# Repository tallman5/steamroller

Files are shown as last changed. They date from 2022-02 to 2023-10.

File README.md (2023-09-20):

# Steamroller

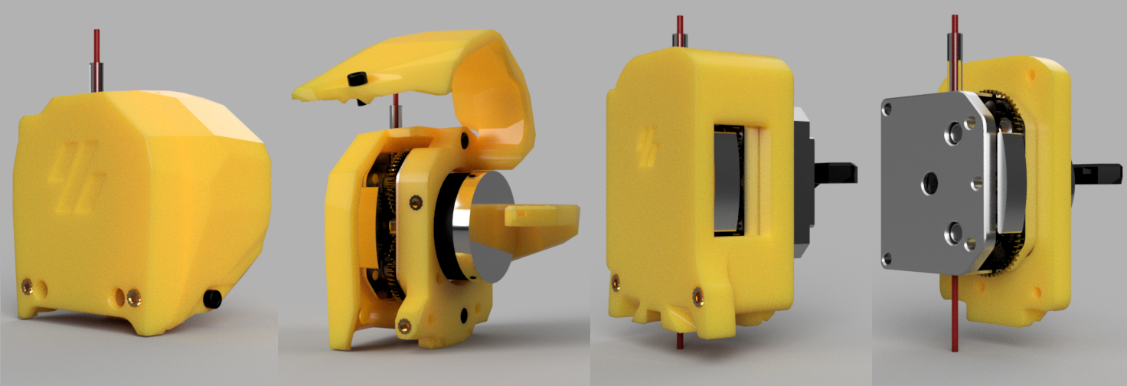
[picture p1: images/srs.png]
OMG Extruder and Steamroller Parts Steamroller


<div style='border: 1px solid #997404; border-radius: 5px; background-color: #fff3cd; padding: 15px; color: #997404;'>
   <strong>Note: </strong>These are still in testing. Please use at your own risk. Create an issue if needed. Thanks!
</div>

## Overview
The Steamroller is a custom adapter to hold the OMG Extruder for various print heads.
The following is a list of the available flavors.

1. Steamroller Stealthburner, SRSB, for the Stealthburner/Clockwork 2
1. Steamroller Afterburner, SRAB, for the Afterburner/Clockwork 1
1. Steamroller EVA, SREVA, you guessed it, for EVA, coming soon!

Print the files in the STL folder for the appropriate version.
The default STLs have a 4.7mm hole for M3x5x4 threaded inserts.
Since the inserts aren't always easy to get, there are subfolders for other size threaded inserts.
For example, the STLs in the folder ti-5-3 has 5.3mm holes for M3x5.5x4 inserts.
Want a different threaded insert size?
Create an issue here and I can create a custom set.

## OMG Extruder Links

This project does not have a donate button.
However, if you order the OMG with an affiliate link, you won't pay more and a small commission will go to this project.
Thank you!

Affiliate Link: [https://amzn.to/48pWOVK](https://amzn.to/48pWOVK)

## Why?
During a Voron 2.4 build, I was using the OMG with a bowden tube on the Voron until the Galileo parts came in.
There were some great prints coming from the OMG extruder.
After installing and tuning the Galileo, I noticed how close the prints were in quality.
So, decided to try to go direct drive with the OMG.
The Steamroller AB is the result.

## Installation Steps
Everything about this is per the Voron standard, slicer settings, heat set inserts, etc..

1. Gather parts from the BOM, there's a BOM for each flavor
1. Print the parts
   1. Yellow's not required :smile:, just used it on renders following the Steamroller theme
   1. Front and back found in the STL folder
   1. The 2- or 3- hole chain anchor from the Voron Clockwork 2 found [here](https://github.com/VoronDesign/Voron-Stealthburner/tree/main/STLs/Clockwork2)
   1. If using the SRSB, the cable cover from the Voron Clockwork 2 found [here](https://github.com/VoronDesign/Voron-Stealthburner/tree/main/STLs/Clockwork2)
1. Add the heat set inserts
1. Install the cable chain anchor to the back
1. For the SRSB, install the cable cover to the back
1. If installing a NEMA17 on the SRAB, push the motor through the back before attaching the motor to the OMG
1. Place the OMG in the Steamroller front
1. Screw the back to the front
1. Install a piece of PTFE for the Steamroller to the hotend
   1. SRAB - Mine was 62mm for a v6 hot end
1. Mount the Steamroller to the carriage
1. Install the fan assembly
1. Edit the printer.cfg, below is what I used with Klipper/Fluiddd/Spider v1.2:
      ```
      # Steamroller AB (SB and EVA should be similar)
     rotation_distance: 47.77753134
     microsteps: 16
     full_steps_per_rotation: 760
     gear_ratio: 3:1
     dir_pin: PD6
     ```
1. Do the e-steps calibration and update the rotation_distance
1. Print something!

## How Well Does It Work?
In the following pic, the Galileo is on the left, SRAB on the right. 
They are printed from the same filament spool using same .gcode file. 
The two were printed one right after the other (SRAB installation in between).

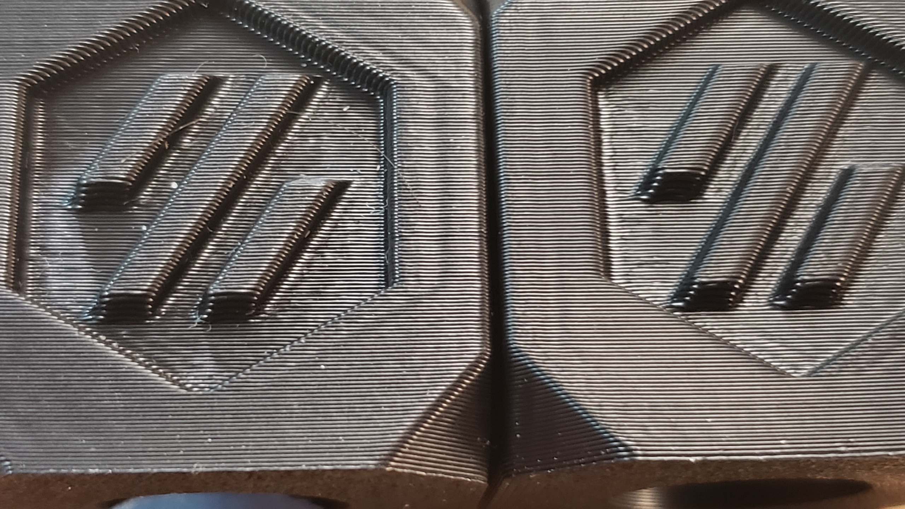
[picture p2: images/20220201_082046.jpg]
Galileo/Steamroller Calibration Cubes


## Got A Request?
Have something you think would be useful?
Feel free to create an issue here for something you may want added.
Such as, threaded inserts for PCBs.
Most of my stuff is at a minimum, so, I may not have added something you'd find useful.

## Enjoy!
If you implement it, send me a pic and I'll share it for others!

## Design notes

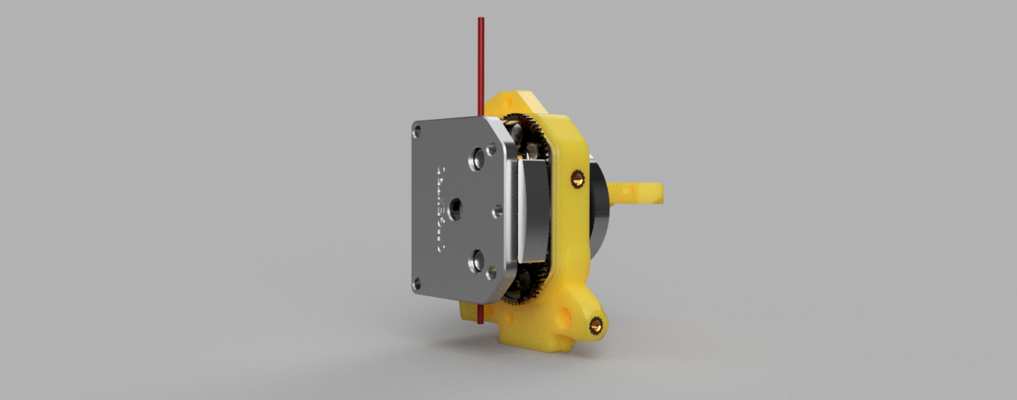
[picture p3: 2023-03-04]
images/sr-03.png

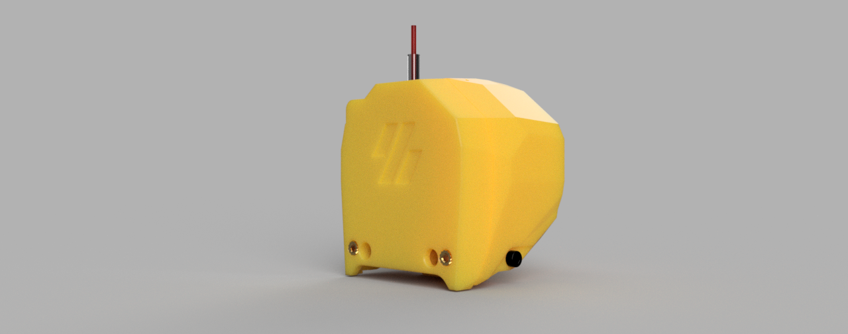
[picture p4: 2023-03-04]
images/sr-01.png

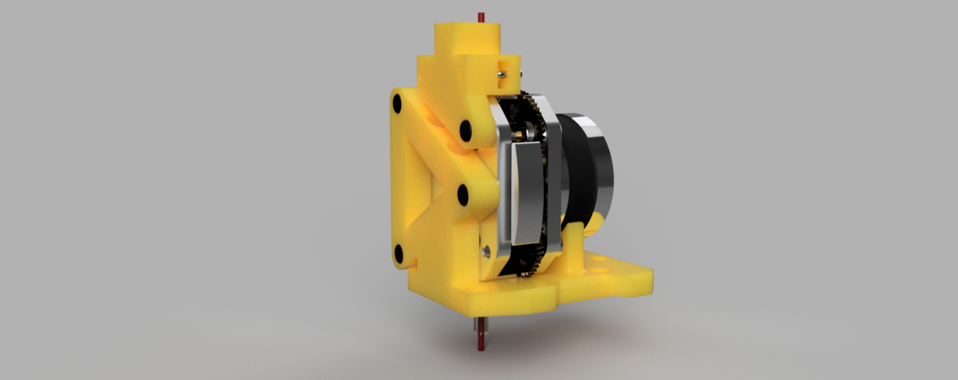
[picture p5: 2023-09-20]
images/sr-12.png

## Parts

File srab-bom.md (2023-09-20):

# Steamroller Afterburner BOM
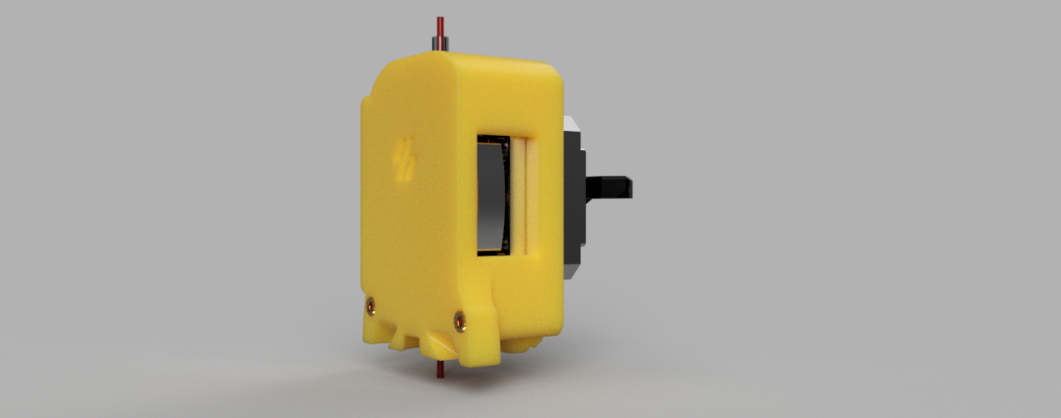
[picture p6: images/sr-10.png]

|Image|Number|Quantity|Description|
|-|-|-|-|
||Chain Anchor (3 Hole)|1|From Voron Clockwork 2: [https://github.com/VoronDesign/Voron-Stealthburner/tree/main/STLs/Clockwork2](https://github.com/VoronDesign/Voron-Stealthburner/tree/main/STLs/Clockwork2)|
||M3x20 SHCS|1||
||M3x5x4 Threaded Insert|12||
||M3x6 SHCS|1||
||M3x8 SHCS|3||
||OMG V2S|1|Affiliate Link: [https://amzn.to/48pWOVK](https://amzn.to/48pWOVK)|
||SRAB Back|1||
||SRAB Front|1||

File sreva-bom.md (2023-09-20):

# Steamroller EVA BOM
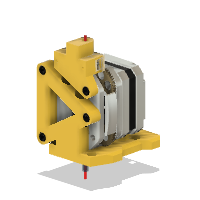
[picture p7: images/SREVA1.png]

|Image|Name|Number|Description|Quantity|
|-|-|-|-|-|
||Disc Magnet 6x3 v3:2|Disc Magnet 6x3|Affiliate Link: [https://amzn.to/3ENL41G](https://amzn.to/3ENL41G)|2|
||Filament Runout Sensor for OMG:1|Filament Runout Sensor for OMG||1|
||Hall Sensor AH3364Q v6:1|Hall Sensor AH3364Q|Affiliate Link: [https://amzn.to/424WQ1N](https://amzn.to/424WQ1N)|1|
||M2 Washer v2:1|M2 Washer||1|
||M2x8 BHCS Self Tapping v3:1|M2x8 Self-tapping Screw|Affiliate Link: [https://amzn.to/3LvqeIu](https://amzn.to/3LvqeIu)|2|
||M3x10 SHCS v3:1|M3x10 SHCS||2|
||M3x25 SHCS v2:1|M3x25 SHCS||3|
||M3x5x4 Threaded Insert v2:1|M3x5x4 Threaded Insert||2|
||M3x8 SHCS v2:1|M3x8 SHCS||1|
||OMG V2S v28:1|OMG V2S|Affiliate Link: [https://amzn.to/48pWOVK](https://amzn.to/48pWOVK)|1|
||SR EVA Bottom:1|SR EVA Bottom||1|
||SR EVA Front:1|SR EVA Front||1|

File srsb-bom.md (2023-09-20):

# Steamroller Stealthburner BOM
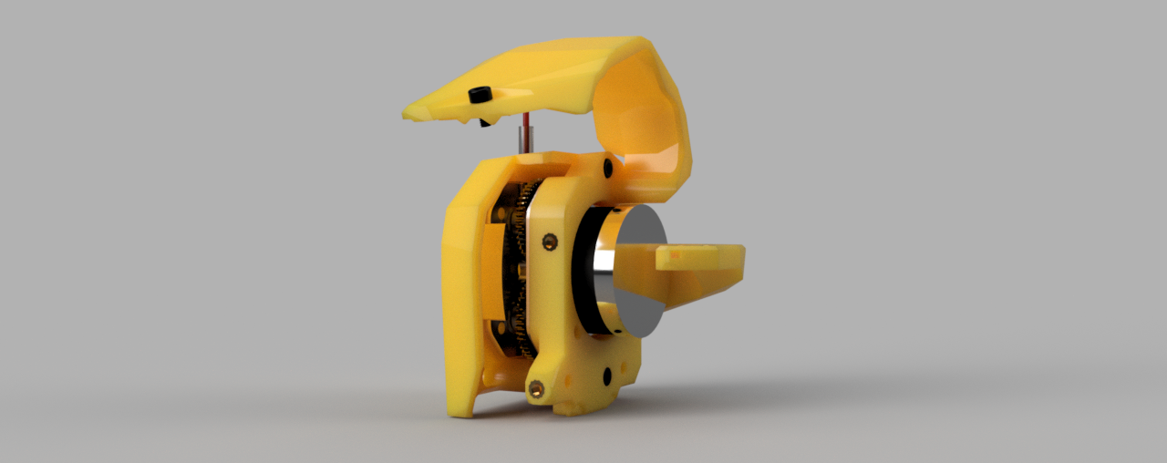
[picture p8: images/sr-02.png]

|Image|Number|Quantity|Description|
|-|-|-|-|
||Cable Cover PCB|1|From the Voron Clockwork 2: [https://github.com/VoronDesign/Voron-Stealthburner/tree/main/STLs/Clockwork2](https://github.com/VoronDesign/Voron-Stealthburner/tree/main/STLs/Clockwork2)|
||Chain Anchor (3 Hole)|1|From Voron Clockwork 2: [https://github.com/VoronDesign/Voron-Stealthburner/tree/main/STLs/Clockwork2](https://github.com/VoronDesign/Voron-Stealthburner/tree/main/STLs/Clockwork2)|
||M3x10 SHCS|1||
||M3x16 SHCS|2||
||M3x5x4 Threaded Insert|11||
||M3x6 SHCS|1||
||OMG V2S|1|Affiliate Link: [https://amzn.to/48pWOVK](https://amzn.to/48pWOVK)|
||SR SB Back|1||
||SR SB Front|1||

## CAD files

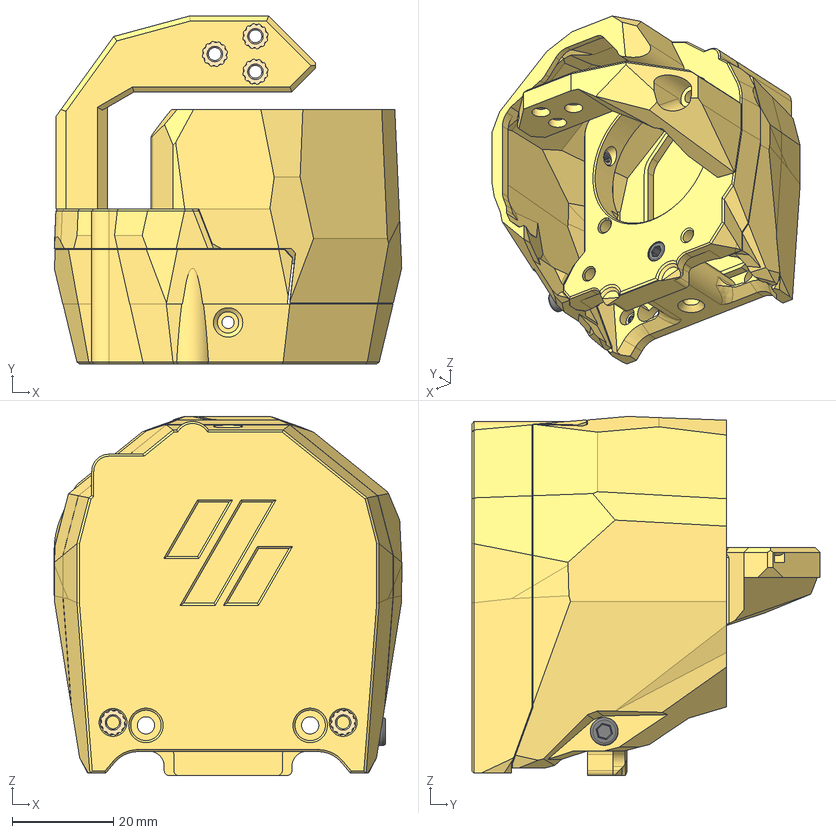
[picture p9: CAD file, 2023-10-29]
cad/SRSB v41.step
68.6 x 68.7 x 70.9 mm
SR SB Back
Cable Cover PCB
Chain Anchor (3 Hole)
SR SB Front
M3 SHC x 4
M3x5x4 Threaded Insert x 12

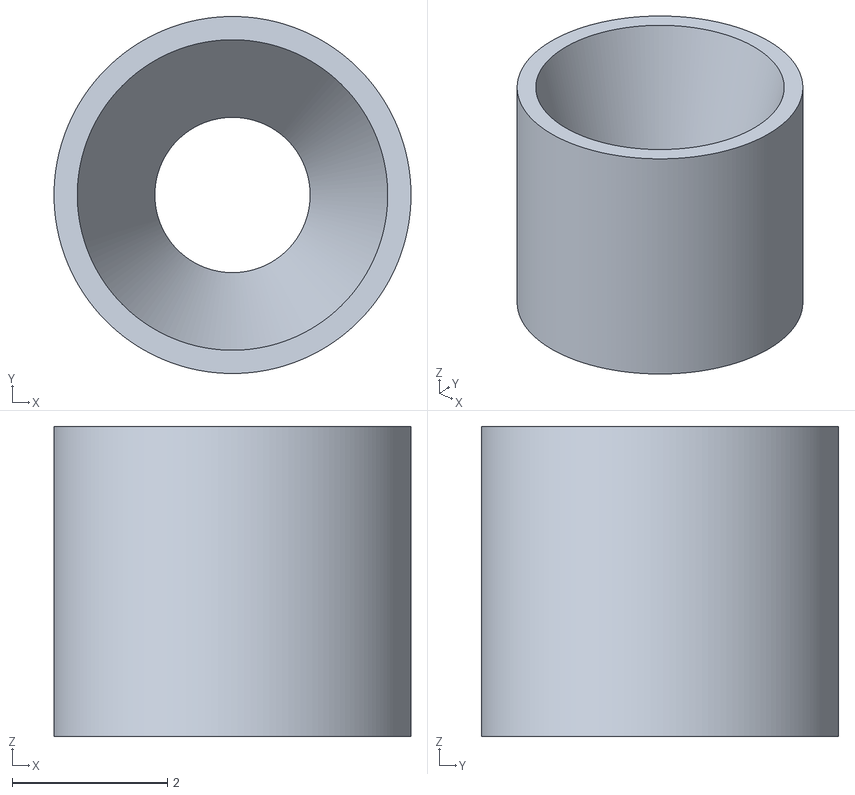
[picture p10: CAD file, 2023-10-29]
stl/omg-funnel.stl
4.60 x 4.60 x 4.00

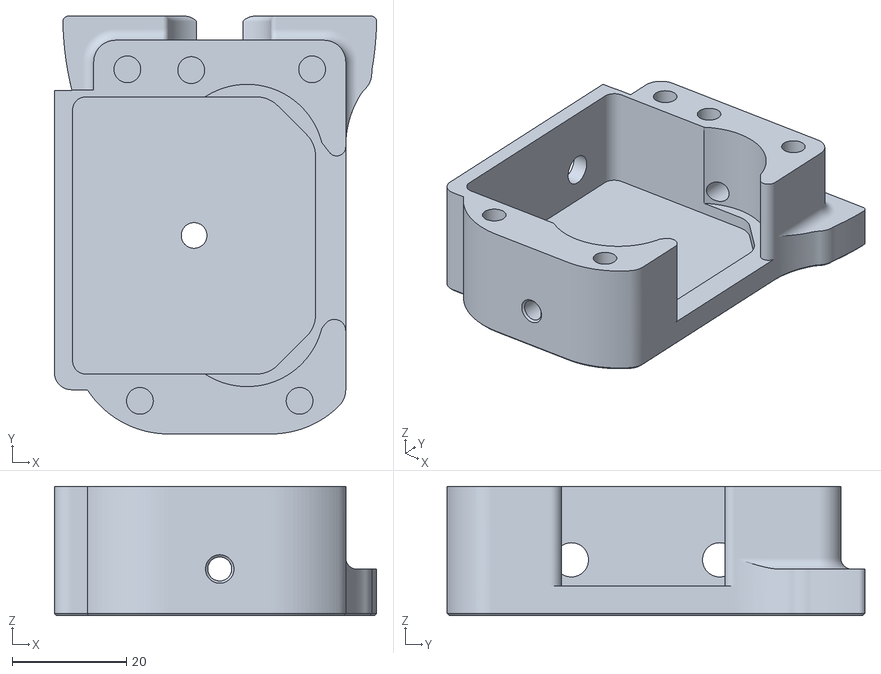
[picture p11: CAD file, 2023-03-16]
stl/srab/sr-ab-front.stl
56.5 x 73.3 x 22.7

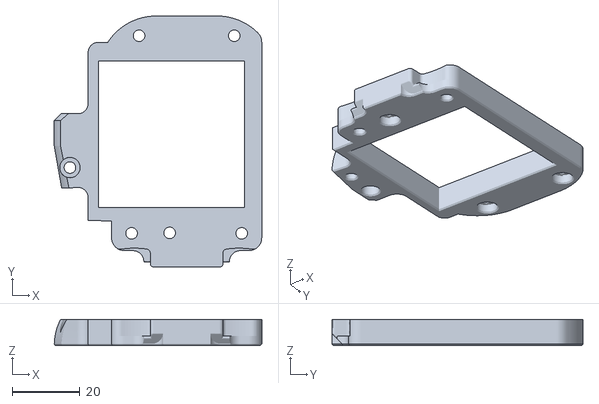
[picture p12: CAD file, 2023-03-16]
stl/srab/ti-5-3/sr-ab-back-5-3.stl
61.1 x 73.9 x 7.70

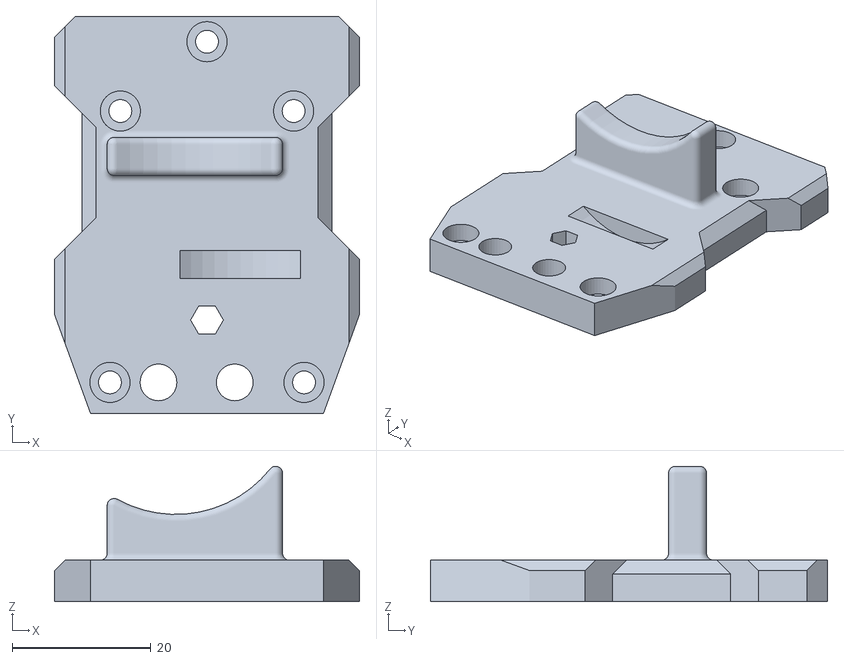
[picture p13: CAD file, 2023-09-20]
stl/sreva/ti-5-3/sr-eva-bottom-5-3.stl
44.0 x 57.3 x 19.5

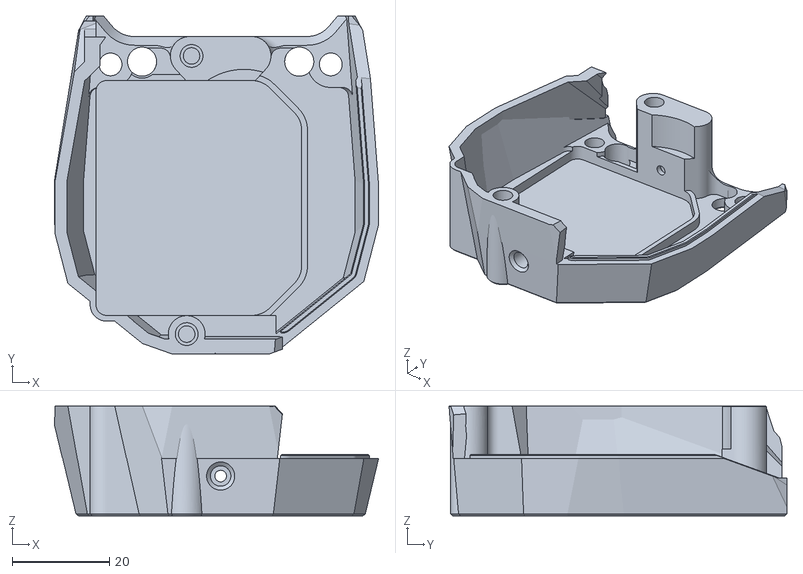
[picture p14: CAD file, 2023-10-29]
stl/srsb/sr-sb-front.stl
66.8 x 69.7 x 22.6

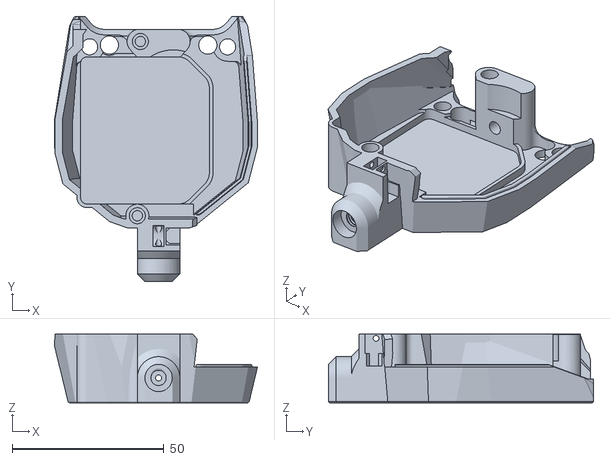
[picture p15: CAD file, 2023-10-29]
stl/srsb/ti-5-3/sr-sb-front-frs-5-3.stl
66.8 x 87.2 x 22.6

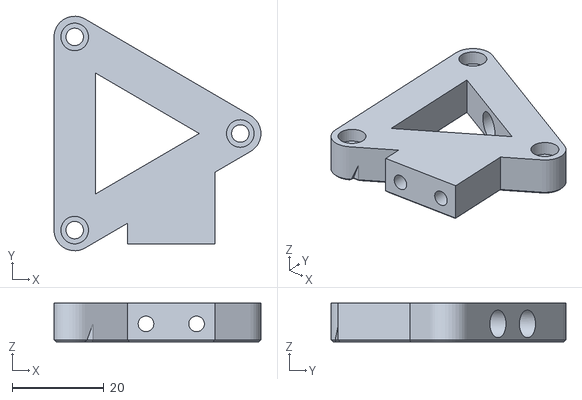
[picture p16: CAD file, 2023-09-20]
stl/sreva/ti-5-3/sr-eva-front-5-3.stl
45.0 x 51.0 x 8.40

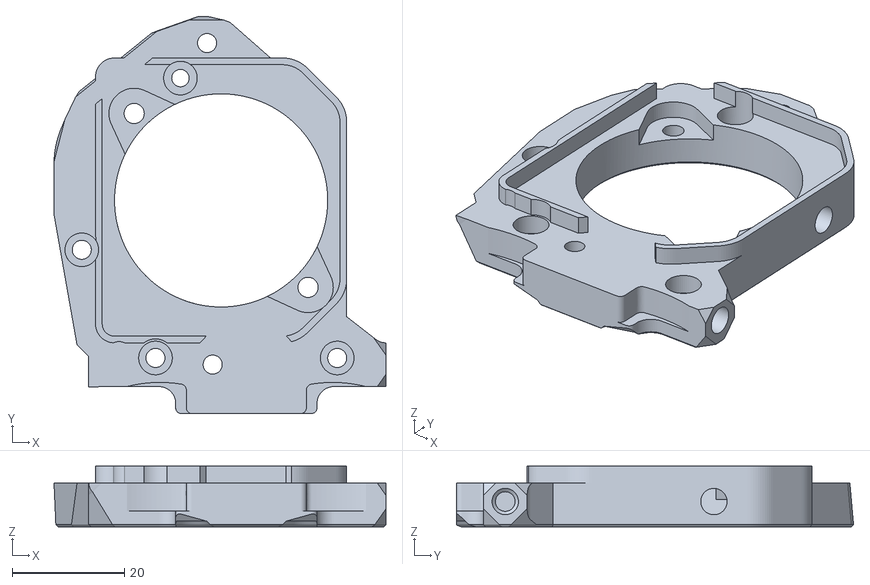
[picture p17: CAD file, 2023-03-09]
stl/srsb/sr-sb-back.stl
59.2 x 70.8 x 10.8

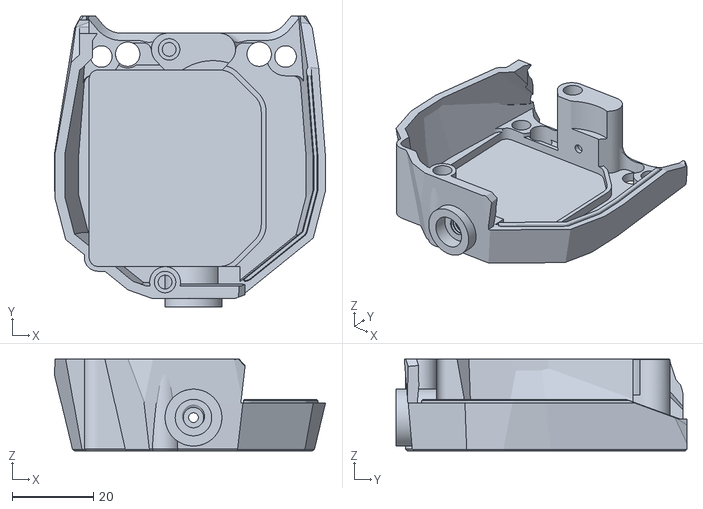
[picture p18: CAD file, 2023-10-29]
stl/srsb/ti-5-3/sr-sb-front-bowden-5-3.stl
66.8 x 71.7 x 22.6

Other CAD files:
stl/srab/sr-ab-back.stl
stl/srab/ti-5-3/sr-ab-front-5-3.stl
stl/srsb/sr-sb-front-frs.stl
stl/srsb/ti-5-3/sr-sb-front-5-3.stl
stl/srsb/ti-5-3/sr-sb-back-5-3.stl
design/steamroller.blend

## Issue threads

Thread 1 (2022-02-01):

Back/motor plate piece too thick for extruder fan housing

tallman5, 2022-02-01:
The back piece needs to be shaved down a bit in order to fit into the carriage. The front of the back piece collides with the fan housing.

tallman5, 2022-02-01:
Current workaround is to use a utility knife and remove some of the plastic.

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

tallman5, 2022-02-01:
added bevel

Closed 2022-02-01.

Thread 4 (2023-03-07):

request: afterburner rear nema17 compatibility

bulcke, 2023-03-07:
It would be really nice to have afterburner rear part that can hold a standard nema17 (42x42mm) stepper motor.
Should be an easy mod, since the screw holes already match. Just the coutout where the stepper sits should be bigger.

The cable chain attachment may have to be reworked. Or you could make a version without that piece sticking out to the rear. Other designs have the chain attached to the stepper instead of the backplate.

If you're ok with it, I'm ready to edit your design myself. But I would need an f3d file.

tallman5, 2023-03-08:
Already adding the cable chain anchor from the Clockwork 2. I can add support for the 42mm stepper. Teaser pic attached.
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

tallman5, 2023-03-09:
@bulcke - do you have a NEMA17 to test it?

bulcke, 2023-03-09:
> @bulcke - do you have a NEMA17 to test it?

I do

tallman5, 2023-03-09:
I'm on Discord, tallman#9584 if you have any questions

Closed 2023-03-09.

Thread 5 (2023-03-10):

Flip the OMG so the button is on the other side

tallman5, 2023-03-10:

tallman5, 2023-03-10:
@bulcke, is this necessary?

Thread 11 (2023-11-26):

On SRAB add a heatset hole for attaching a AB's cable cover.

josef-jelinek, 2023-11-26:
This may require flipping the release button to the other side and if aligned with the tension adjustment holes also updating the cable cover...

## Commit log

2021-12-13 adding existing files
    [bowden_module_front.3mf, bowden_module_front.stl, bowden_module_rear_generic.3mf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]
2021-12-13 adding blend
    [steamroller.blend]
2021-12-17 adding omg
    [bowden-bottom.stl, bowden-top.stl, bowden_module_front.3mf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]
2021-12-19 updating clockwork
    [bowden-bottom.stl, bowden-top.stl, bowden_module_front.stl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]
2021-12-29 added origs
    [clockwork.blend, extruder_body.3mf, extruder_body.stl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]
2022-01-05 updating back
    [extruder_body.3mf, extruder_body.stl, extruder_motor_plate.3mf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]
2022-01-20 updating block
    [bowden_module_front.stl, bowden_module_rear_generic.stl, bowden_module_rear_igus.stl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]
2022-01-20 udpated front
    [bowden_module_front.stl, bowden_module_rear_generic.stl, bowden_module_rear_igus.stl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]
2022-01-21 correcting voron originals
    [bowden_module_front.stl, bowden_module_rear_generic.stl, bowden_module_rear_igus.stl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]
2022-01-21 updated cw front
    [clockwork-block.stl, clockwork-front.stl, clockwork.blend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]
2022-01-21 updated block rear
    [clockwork-rear-generic.stl, clockwork-rear.stl, clockwork.blend]
2022-01-21 updated folder structure
    [bowden_module_front.stl, bowden_module_rear_generic.stl, extruder_body.stl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]
2022-01-24 sync STLs
    [chain_anchor_generic.stl, chain_anchor_igus.stl, clockwork-front.stl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]
2022-02-01 beveled motor plate to fit in fan housing
    [steamroller-rear-generic.stl]
2022-04-26 updating docs
    [bowden_module_front.stl, bowden_module_rear_generic.stl, chain_anchor_generic.stl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]
2023-03-04 updating with sr-sb
    [sr-ab-front.stl, sr-ab-rear.stl, sr-sb-back-5-3.stl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]
2023-03-09 adding srab and srsb
    [sr-ab-back-5-3.stl, sr-ab-back.stl, sr-ab-front-5-3.stl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]
2023-03-11 added holes for tension adjustment
    [sr-ab-front-5-3.stl, sr-ab-front.stl]
2023-03-16 added hole to front, removed artifact
    [sr-ab-back-5-3.stl, sr-ab-back.stl, sr-ab-front-5-3.stl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]
2023-09-20 updating BOMs
    [sr-eva-bottom-5-3.stl, sr-eva-front-5-3.stl]
2023-10-29 updating front
    [SRSB v41.step, omg-funnel.stl, sr-sb-front-5-3.stl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]
